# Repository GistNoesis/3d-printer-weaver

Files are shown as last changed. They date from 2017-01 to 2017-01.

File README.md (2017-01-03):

# 3d-printer-weaver
Empower your 3d-printer with string art.

Happy New Year 2017 :)

This project won't be developped further anytime soon, but If you'd like to support us, you can do so at our website. https://gistnoesis.net

#TLDR: Look at the images. How to use the soft at the bottom. How to use a 3d printer to weave. The thiner the thread the better. Multiple small improvements have a large impact.

#The story :

I saw https://github.com/theveloped/ThreadTone last week on HN, and decided I could mod my 3d printer as a 3 day week-end project, to do the same thing.
I have a Taz-4 but it should work with a lot of open-source printers.
Because the workarea is smaller with a 3d printer than with a laser cutter, it presented quite a few interesting challenges to miniaturize its solution.
On the other hand, as I'm printing the circular loom, it's already precisely positionned, and I can have tighter clearances.

I started the first day and achieved pretty promising results quite quickly.
I used openscad to design the circular loom. 
I began with 50 2mm height, 1mm radius, pillars in a 70mm radius ring, and wrote a simple algorithm to generate the trajectory of the head.
To feed the thread I used an old pen ink plastic tube (3mm wide), which I taped to the printer head.

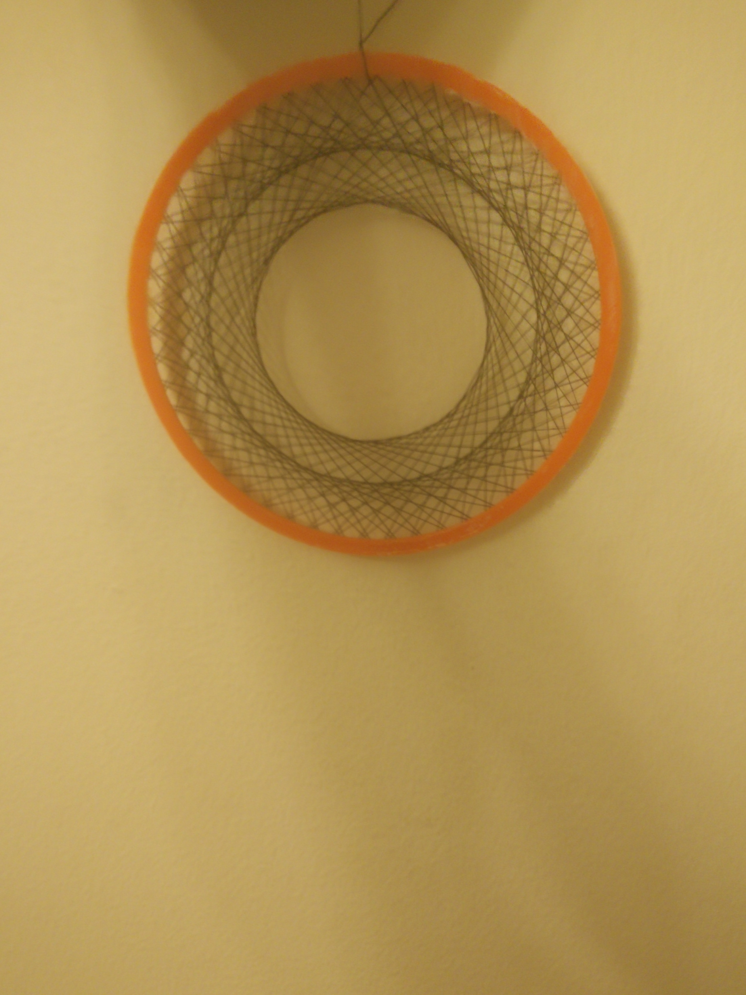
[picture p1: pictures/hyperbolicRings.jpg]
Prime Rings


It has 100 lines it is a symetric desgn which was constructed algorithmically, by choosing the distance between consecutive pillars (13, and 17) so that they are coprime with the number of pillars, so we touch all pillars exactly one time.

On the second day, I worked on being able to weave an image. 

Quickly I realized that the original ThreadTone project, needed at least 150, (300 better) anchor points to have correct results.
Also the algorithm used in ThreadTone is far from being optimal, as some ThreadTone comments revealed there is an alternative project 

https://github.com/danielvarga/string-art which uses a mathematical technique (solving a linear equation) to obtain the optimal result when the wires are infinitely thin.

string-art needs its input in greyscale negative (on ubuntu we can use : convert -negate -colorspace gray imginput.jpg imgoutput.jpg) to obtain the correct input.

input :
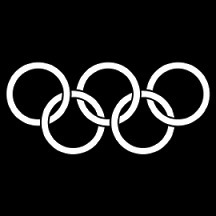
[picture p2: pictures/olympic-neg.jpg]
Olympic input input to string-art


output :
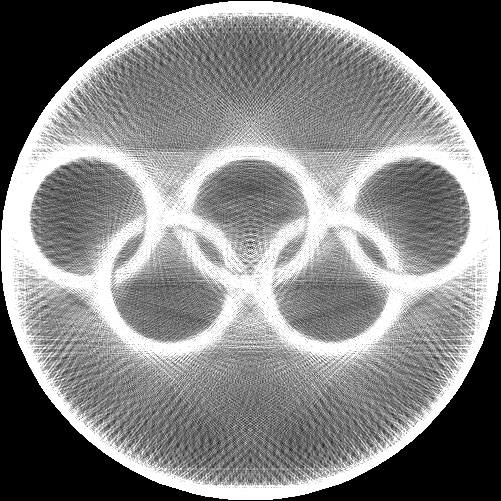
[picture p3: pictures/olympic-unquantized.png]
Result output of string-art


We can draw more detailed images too :

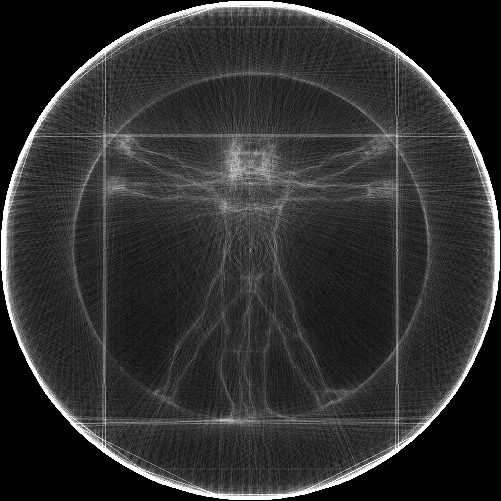
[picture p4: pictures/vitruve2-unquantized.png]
Vitruve


I decided to use string art. It produces a graph of around 3000 edges as a result, and not all lines have the same darkness so it means that some lines must be repeated to increase the contrast.
String art use a quantisation formula to convert the floating point results of the linear solver, into a discrete number of thread. 
But when there is high contrast it happens that some times the edge must be repeated 15 times, which poses problem during manufacturing.

After trying a few times to modify the quantisation algorithm. I choose to reduce the number of edges by using a sampling strategy, montecarlo fashion. 
This technique also permits me to choose the number of edges, and allows for probabilistically accurate reducing of the number of edges. It also means we could continue add edges to a current weaving by overlaying a new graph on top of a previous graph.
I increased the number of pillars to 150 with a 70mm radius ring. And tried to weave. 

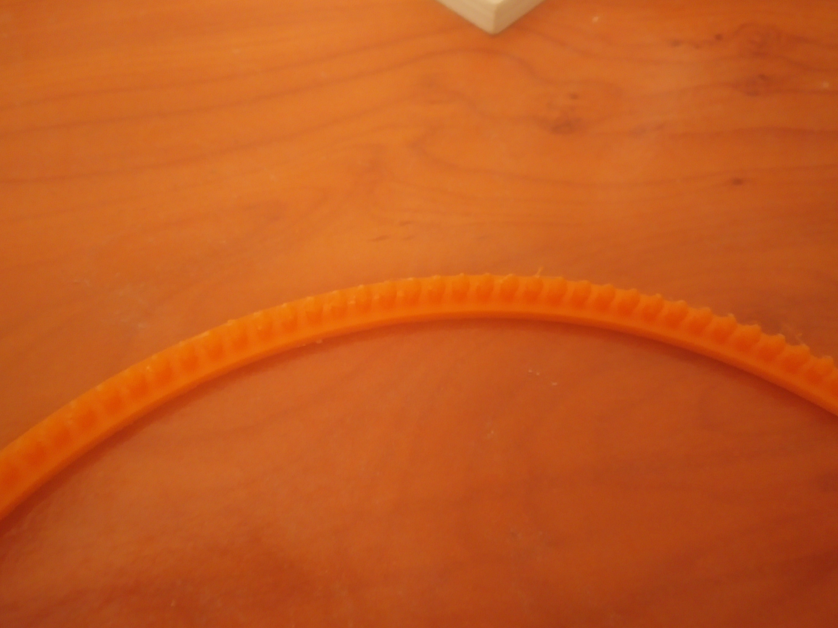
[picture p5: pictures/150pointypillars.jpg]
150 pointy pillars 150 pointy pillars in a 70 mm radius ring


Because of the number of pillars and the small size of the ring, it means that there is less than 1mm between the pillars. So the thread guide can't cross. So it must jump over the pillars, go down, hook the pillar, then up again, jump the pillar, then down again.
I tweaked my trajectory algorithm to take this into account. It kind of work and succeded to hook the pillars 3 out of 4 times, which means than when you have thousand of pillars to hook that it won't work.
The flexible ink-pen tube, and tape, was not precise enough.

So I looked for an alternative guide. Luckily I found a needle to inflate soccer balls. It was 2mm wide, and had a hole all the way though so I can pass a needle through it to insert the thread into it.
To attach the needle to the printing head I tried tape, but it proved ineffective. So I designed a needle holder in openscad :
A 10mm cube with a hollow cylinder in the middle. And printed it, to attach it to the head, I remarked that when the printing head is still hot ABS will stick to it. 

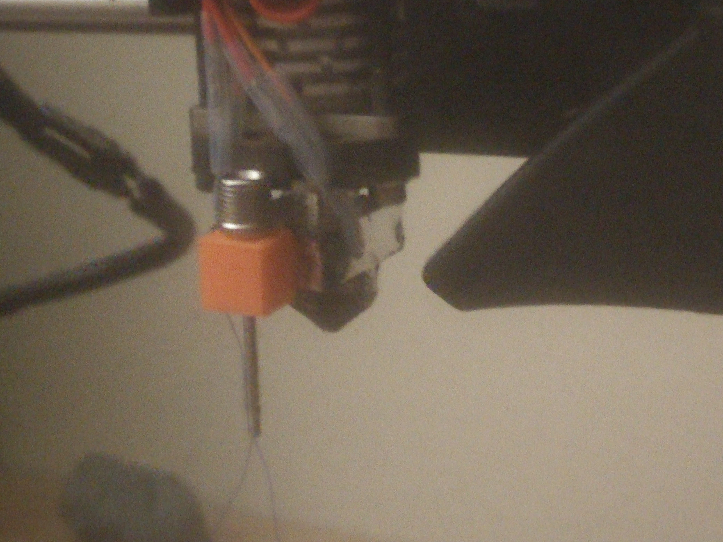
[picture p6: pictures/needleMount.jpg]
Needle Mount Mounting the needle to the hot head


The needle fit is quite tight (automatically adjusted by the hot head trick). The needle must be below the printing head so the printing head don't hurt the pillars, and not to far from the printing head so that it don't reduce the print area much.
Also when homing the printer, the needle fit should not be so strong that it would break the glass plate. But it turns out it worked just right.

After these adjustments, It worked better, but not quite well enough. In particular as more and more threads go in, it becomes harder to add more without tripping other wires. 

At the end of the second day, results were unsatisfactory, but the needle holder was a very definite improvement. It also reveals some problems: when I add to much thread it becomes too dark, and we can't see through anymore. 

On the next day, I decided to mitigate those two problems with one stone. Increasing the ring size. It now is 110mm radius, with the 150 pillars the needle can go between without the need to jump, with a 0.5mm clearance. 
It worked better, but there were some visual artifacts (mainly blurryness but which is important because the effect we are trying to observe are subtle), because the pillars are of the same order of size as the distance between them, the approximation of them as a single point don't hold. So instead for each pillar I now have two anchor points,
either the top side or the bottom side of the pillar. Which means that with 150 pillars, I can have the equivalent of a "300 anchor points" resolution.

I had to tweek string-art to add these unevenly spaced anchor points.

I adapted the algorithm to the increase resolution and weaving constraints. 
The weaving was fine but it became too dark as lines where added. 
So I used a smaller diameter polyesther thread, normally used for sewing machines. It immediately worked a lot better.

I tried to weave 800 lines which was a length of 196 meters, I have a 200 meters roll, I had to stop at 61% so around 500 lines, because the needle was starting to trip the wires (it can probably be mitigated by augmenting the z of the needle thoughout the weave and increasing the height of the pillars). Also some pillar broke due to repetitive pulling (more precisely were deformed enough that the needle touched them on the next travel) ,  
The results could also be improved by using even more thin threads, some wider, and taller pillars, but a little less of them.

Here is what I obtain :

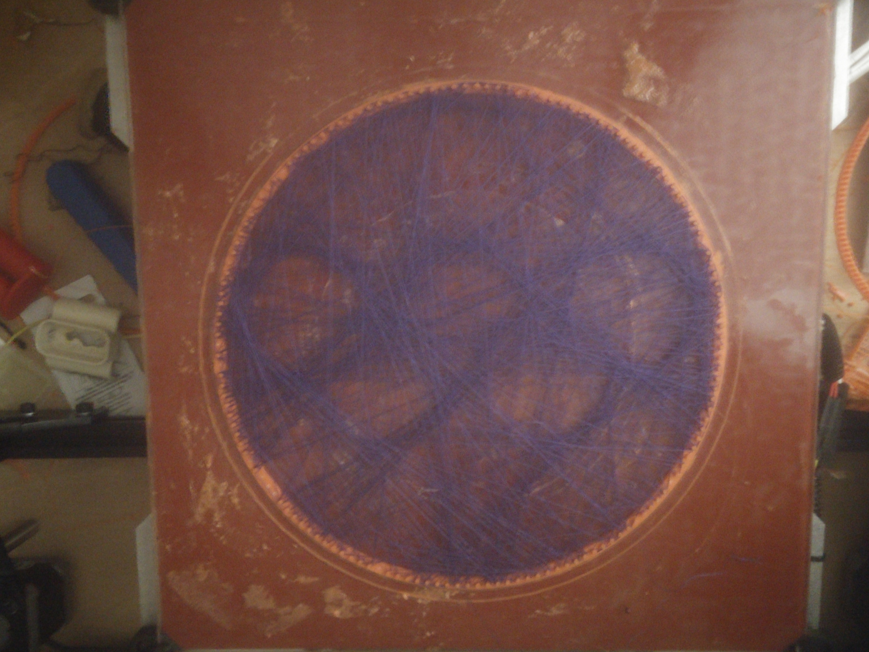
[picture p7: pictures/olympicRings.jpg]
Olympic Rings


Lots of possible improvements can be made.
To go further :
http://www.sosafresh.com/3d-weaver/
https://www.youtube.com/watch?v=iFLZEnoDHe8

#Here's how to use the soft :

dependencies :
pip install numpy matplotlib pylab

use my version of string-art it has 150 pillar and 1mm pillar radius hardcoded (inside the "atan" ), so 300 anchor points, you can also adjust the hardcoded shrinkage to increase or reduce the size of the image :

python string-art.py input.jpg output-prefix          #it takes 5 min using a single core, although it is much faster with 2*less pillars (probably an issue with the original string-art using dense matrix instead of sparse matrix in the solver)

then use ipython 

import wiring
l,g = wiring.loadGraphFromFile( "output-prefix-unquantized.txt", brokenPins , 40, nbEdges ) # use brokenPins = {} if no pins are broken, or set the broken pillars hardcoded in wiring.brokenPin() and pass this dictionary

you can then view the graph with 

wiring.displayGraph2( 150, g, 110, linewidth = 0.1)  # 150 = number of pillars

traj = wiring.generateGraphTrajectory2( g , 150, radius_of_the_ring, 3.0 ) #3 = 1.2mm pillar radius + 1mm radius head tool + 0.8mm clearance

wiring.writeGcode( traj, outname ) 

I have a LulzBot Taz4 so I emmitted some marlin gcode, but it's pretty standard and should work anywhere, I don't set speed in it so set your speed in your printer interface)
#The Gcode positioning is relative so we can precisely position the needle to take into account the offset between hothead and needle

To 3d-print you can use openscad to generate the STL from the scad file.
Then you slice it with slicer.
Then you 3d print and leave the part in place.
While the hot head cools you stick the needle holder to it

At the end of the 3d print you manually move the needle (with the thread through it) so that the bottom of the needle is exactly between the two rightmost pillars
 (theta=0, r= radiusof the ring,z = 1.5mm above the ring), it should be below the top of the pillar able to move 1mm  down without touching the ring.

You attach the thread to the pillar 0, one pillar in the counter clockwise from the needle. 
You load the gcode, and print.  For your first tries you can increase z so it moves over the pillar without touching them to check that everything is OK.
 (If it is going slow, set the "modal" speed by doing a fast back and forth ( +10 -10 ) of the head to make it switch to fast mode. )

Additional tip : if the wire is not broken and the weaving failed you can rewind the thread quickly (lift the needle 10 cm above the center of the ring and rewind), so you can try again. 
I left a lot of dead code in the code source so you can follow my train of thought.

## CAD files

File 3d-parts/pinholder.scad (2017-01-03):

difference()
{ cube( [10,10,10],center =true);
  cylinder( r=1.3,h=20,center=true,$fn=100);
}

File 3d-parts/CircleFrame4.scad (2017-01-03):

module ring( r,h,w )
{
difference()
{
    ir = r-w/2.0;
    or = r+w/2.0;
    cylinder( h= h, r1=or, r2=or,center=false,$fn=200);
    translate([0,0,-0.5]) cylinder( h=h+1,r1=ir,r2=ir,center=false,$fn=200);
}
}


module pillars( r, h, nb, offset = 0.5 )
{
    dtheta = 360.0 / nb; 
    for ( i = [0:nb] )
    {
        thetai = dtheta * (i+offset) ;
        x = r * cos(thetai);
        y = r * sin(thetai);
        rmid = 1.1;
        translate( [x,y,h/2]) 
            cylinder( h=h, r1 = 1.0, r2=rmid, center = true, $fn=10);
    }
    
}

r = 110;

ring( r,2,5);

translate( [0,0,2] ) pillars( r, 2, 150,0.5);
//translate( [0,0,2] ) pillars( r-1.5, 2, 75,0.0);
//translate( [0,0,2] ) pillars( r+1.5, 2, 75,0.5);
